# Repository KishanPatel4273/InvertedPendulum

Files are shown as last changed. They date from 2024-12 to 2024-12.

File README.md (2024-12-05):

# Inverted Pendulum on Cart

In InvertedPendulum.pdf lagrange mechanics is used to derive the dynamics of the system. Then A controller is designed.

## Materials

| Quantity | Item | Cost | 
|---|---|---|
| 12x | [100mm V Slot 2020 Aluminum](https://www.amazon.com/dp/B0B7DVN34Y?ref=ppx_yo2ov_dt_b_fed_asin_title&th=1) | 35.97 |
| 2x | [8mm x 400mm Aluminum rod](https://www.amazon.com/dp/B08JGD9F5P?ref=ppx_yo2ov_dt_b_fed_asin_title) | 11.99 |
| 4x | [8mm Aluminum rod support](https://www.amazon.com/dp/B0CWV45879?ref=ppx_yo2ov_dt_b_fed_asin_title&th=1) | 8.99  |
| 1x | [pulley system](https://www.amazon.com/dp/B07MF6TDHF?ref=ppx_yo2ov_dt_b_fed_asin_title) | 14.19 |
| 20x | [(8mm x 22mm x 7mm) (608 2RS) ball bearings](https://www.amazon.com/dp/B09PKD8QZZ?ref=ppx_yo2ov_dt_b_fed_asin_title&th=1) | 6.99  |
| 1x | [Stepper Motor](https://www.amazon.com/gp/product/B0B8HB5N4S/ref=ox_sc_saved_title_2?smid=AWQBCGWISS7BL&th=1) | 16.99
| 1x | [Rotary Encoder 600p/R](https://www.amazon.com/Taiss-Incremental-Encoder-Voltage-Warranty%EF%BC%89600P/dp/B07MX1SYXB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) | 18.99

| Quantity | Part
|---|---|
| 2x | [Cart.stl](/Model-V1/Cart.stl) |
| 1x | [Plate.stl](/Model-V1/Plate.stl) |
| 1x | [PulleyStand.stl](/Model-V1/PulleyStand.stl) |
| 1x | [BearingToPulleyPin.stl](/Model-V1/BearingToPulleyPin.stl) |
| 1x | [EncoderMount.stl](/Model-V1/EncoderMount.stl) |
| 1x | [PendulumMount.stl](/Model-V1/PendulumMount.stl) |
| 1x | [Pendulum.stl](/Model-V1/Pendulum.stl) |
| 1x | [StepperMotorMount.stl](/Model-V1/StepperMotorMount.stl) |
| 1x | [StepperMotorAdapter.stl](/Model-V1/StepperMotorAdapter.stl) |

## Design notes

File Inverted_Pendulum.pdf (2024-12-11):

# Inverted Pendulum

Kishan Patel

December 11, 2024

## 1 Introduction

## 2 Lagrange Mechanics

d
dt

∂L
∂q˙i

−

∂L
∂qi
= Fi with L = T − V | (1)

### 2.1 Finding the Lagrangian

T = Ttransitional + Trotational
= Tc + Tw + Twr

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
The velocity vectors are in reference to the center of gravity, I will assume that the density of each component is constant. Hence, the rod’s center of gravity is at 1
2

l and the weight’s, at the end of the rod, center of mass is at l.

vc =

x˙
0

vw =

x˙ + l

˙θ cos θ
−l

˙θ sin θ

| (3)

Velocity squared is v

2 = v · v

v

2
c = ˙x

2

v

2
w = ˙x

2 + 2lx˙

˙θcosθ + l

2 ˙θ
2

cos²
θ + l

2 ˙θ
2

sin²
θ

= ˙x

2 + 2lx˙

˙θcosθ + l

2 ˙θ
2

(4)

Now, simplify kinetic energy: T

T =

1
2

mcx˙

2

+

1
2

mwx˙

2 + mwlx˙

˙θcosθ +

1
2

mwl

2 ˙θ
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
[mc + mw] + lx˙

˙θ cos θmw +

1
2

l

2 ˙θ
2
[mw +

Iw
l

2

]

(5)

Now, will solve for the potential energy: V.

V = Vw
= mwgl(1 − cos θ)

(6)

Now, we can define the Lagrangian and solve for the mechanics with q1 = x, and q2 = θ.

L =

1
2

x˙

2

[mc + mw] + 1
2

l

2 ˙θ
2
[mw +

Iw
l

2

] + lx˙

˙θ cos(θ)mw − mwgl(1 − cos(θ))

=

1
2

x˙

2
[mc + mw] + l

2 ˙θ
2mw + lx˙

˙θ cos(θ)mw + mwgl cos(θ) − mwgl

(7)

q1 = x :

d
dt

∂L
∂x˙

=

∂L
∂x + Fx

d
dt( ˙x[mc + mw] + l mw

˙θ cos (θ)) = Fx

x¨[mc + mw] + lmw

¨θ cos(θ) − lmw
˙θ
2
sin(θ) = Fx

(8)

q1 = θ :

d
dt

∂L
∂ ˙θ

=

∂L
∂θ
d
dt(2 mw

˙θ l² + mw x˙ cos (θ) l) = −g l mw sin (θ) − l mw

˙θ x˙ sin (θ)

2mw

¨θl² + mwx¨ cos(θ)l − mwx˙

˙θ sin(θ)l = −g l mw sin (θ) − l mw

˙θ x˙ sin (θ)

2mw

¨θl² + mwx¨ cos(θ)l = −glmw sin(θ)

(9)

Since, the pendulum weight is being modeled as point mass Iw
l

2 = mw. sub in ¨x into ¨θ. Now, sub ¨θ back into ¨x Using Matlab syms to simplify even more.

x¨ =

2 l mw sin (θ)

˙θ
2 + 2 Fx + g mw cos (θ) sin (θ)

−mw cos (θ)

2 + 2 mc + 2 mw

¨θ = −

l mw cos (θ) sin (θ)

˙θ
2 + Fx cos (θ) + g mc sin (θ) + g mw sin (θ)

l

−mw cos (θ)

2 + 2 mc + 2 mw

(10)

To make the system more accurate, add friction terms −δcx˙ and −δp

˙θ to ¨x and ¨θ respectively.

## 3 State Space Formulation

Let x =

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
, and Fx = u | (11)

x˙ =

x˙
x¨
˙θ
¨θ

=

x2

2 l mw sin(x3) x4

2+2 u+g mw cos(x3) sin(x3) −mw cos(x3)

2+2 mc+2 mw
x4
−

l mw cos(x3) sin(x3) x4

2+u cos(x3)+g mc sin(x3)+g mw sin(x3) l(−mw cos(x3)

2+2 mc+2 mw)

= f(x, u) | (12)

### 3.1 linearization about fixed point

Now, find states to linearized at f(x, u) = 0

f(x, u) = 0

f([x1, 0, x3, 0]T
, 0) =

0

g mw cos(x3) sin(x3)
−mw cos(x3)

2+2 mc+2 mw
0
−

g mc sin(x3)+g mw sin(x3)
l(−mw cos(x3)

2+2 mc+2 mw)

(13)

f(x, u) = 0 when x1 ∈ R, x2 = 0, x3 = πn ∀n ∈ Z, x4 = 0, and u = 0.

x¯ =

x1
0
πn = 0
0

(14)

Now, we are ready for the state space equation ˙x = Ax + Bu. To find the matrices A and B we will take the Jacobian of f(x, u). For the model, we will want x3 to be 0 as that is the upright position of the pendulum.

x˙ = ∂xf

[x1,0,0,0]T ,0

(x − x¯) + ∂uf

[x1,0,0,0]T ,0

(u − 0)

x˙ =

0 | 1 | 0 | 0
0 −δ
| | g mw 2 mc+mw | 0
0 | 0 | 0 | 1
0 −δ −
| | g mc+g mw l (2 mc+mw) | 0

(x − x¯) +

0
2
2 mc+mw
0
−

1
l (2 mc+mw)

u

y = Cx

(15)

Now, we have our state space equation and measurement equation. The δ term is friction of the cart moving horizontally.

### 3.2 Controllability

The rank(-

B AB A²B A³B
) = 4; therefore, we have full controllability of the system with our control Fx = u.

### 3.3 Observability

C =

1 0 0 0
(16)

To actualize the system, I will take the simplest case where the sensors will capture the positional state x1 = x only. Now calculate the rank Observability matrix to see if the system is full state observable from just the position of the cart.

O =

C

T AT C

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
(17)

The rank of the Observability matrix is 4; therefore, we can estimate all the other states.

## 4 Controller with C = I

### 4.1 Proportional Control

For the proportional control let u − u¯ = −K(x − x¯).

x˙ = Ax + Bu
x˙ = Ax − BKx
x˙ = (A − BK)x

(18)

Since the system is controllable, the matrix K can be placed so that A − BK can have any eigenvalues. Now what eigenvalues should one choose? λi ∈ {z ∈ C : Re(z) < 0}. But, what is the optimal choice? For this, the Linear Quadratic Regulator (L.Q.R.) will be used. Define the cost J which is a quadratic function in x and u.

J =

Z ∞

0

x

T Qx + u

T Ru dt

x˙ = Ax + Bu

Q =

1 | 0 | 0 | 0
0 10 | 0 | 0
0 | 0 | 10 | 0
0 | 0 | 0 | 100

R =

1

(19)

Now finding the minimum of the cost function is all done for us in Matlab. Kr = lqr(A, B, Q, R). The interpretation of Q and R is that it defines the cost of controlling specific states.

### 4.2 Integral Control

For the proportional control let u − u¯ = −KI

R t
0

(x − x¯)dt.

w =

Z t

0

(x − x¯)dt

w˙ = x − x¯
w(0) = 0

(20)

To implement integral action set up a new state w which will update with the following discrete rule wn = wn−1 + ˙wndt. The internal gain KI = [.1, .1, .1, .1].

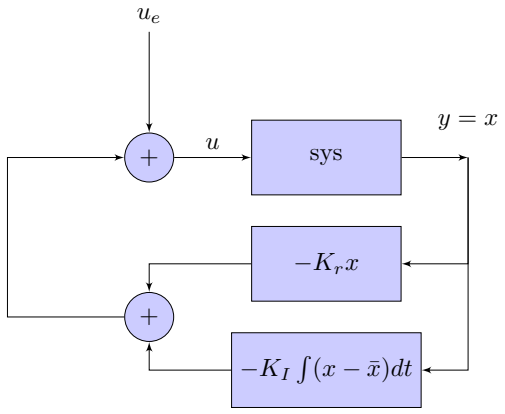
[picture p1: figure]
sys; −Krx

## 5 Controller with C =

1 0 0 0

Since the controller has access to only the positional state, an estimator must be built to estimate other states.

### 5.1 Estimator

A system needs to build that will give us ˆx. The estimate ˆx needs to approach the actual state x. So the error e = x − xˆ needs to approach 0.

e = x − xˆ
e˙ = ˙x − ˙xˆ

e˙ = Ax + Bu − (Axˆ + Bu + f) e˙ = A(x − xˆ) − L(y − yˆ)
e˙ = (A − LC)e

(21)

So if L can be placed such that A − LC has negative eigenvalues, then the estimator will approach the actual state, that is, if the observability matrix has full rank.

˙xˆ = Axˆ + Bu + L(y − yˆ)

yˆ = Cxˆ

(22)

### 5.2 Kalman Filter

The matrix L needs to be chosen optimally to make the estimator. Let Vd be the covariance matrix for the disturbance in the system, and let Ln be the covariance matrix for the noise in the measurement.

x˙ = Ax + Bu + wd
(23)

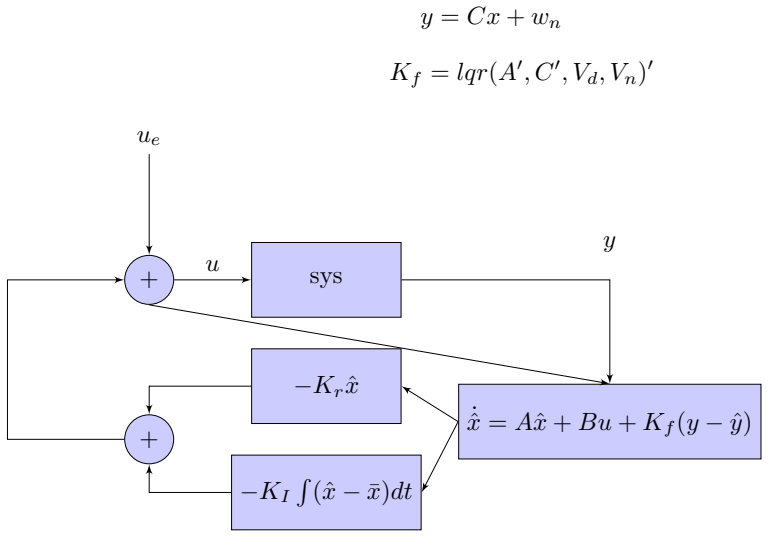
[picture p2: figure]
Kf = lqr(A; sys; −Krxˆ; ˙xˆ = Axˆ + Bu + Kf (y − yˆ)

(24)

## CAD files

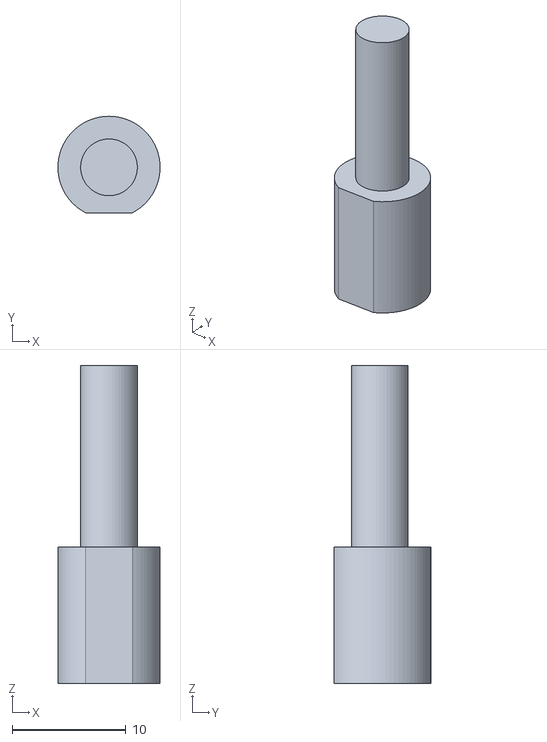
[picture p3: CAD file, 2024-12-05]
Model-V1/StepperMotorAdapter.stl
9.00 x 8.50 x 28.0

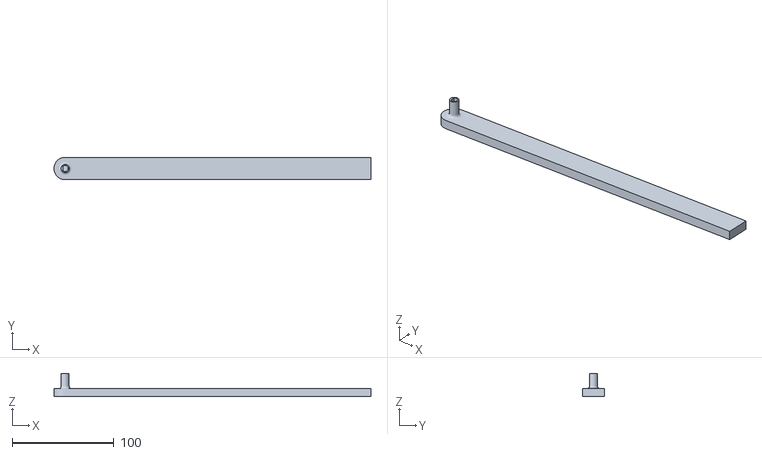
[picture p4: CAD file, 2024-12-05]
Model-V1/Pendulum.stl
311.0 x 22.0 x 23.0

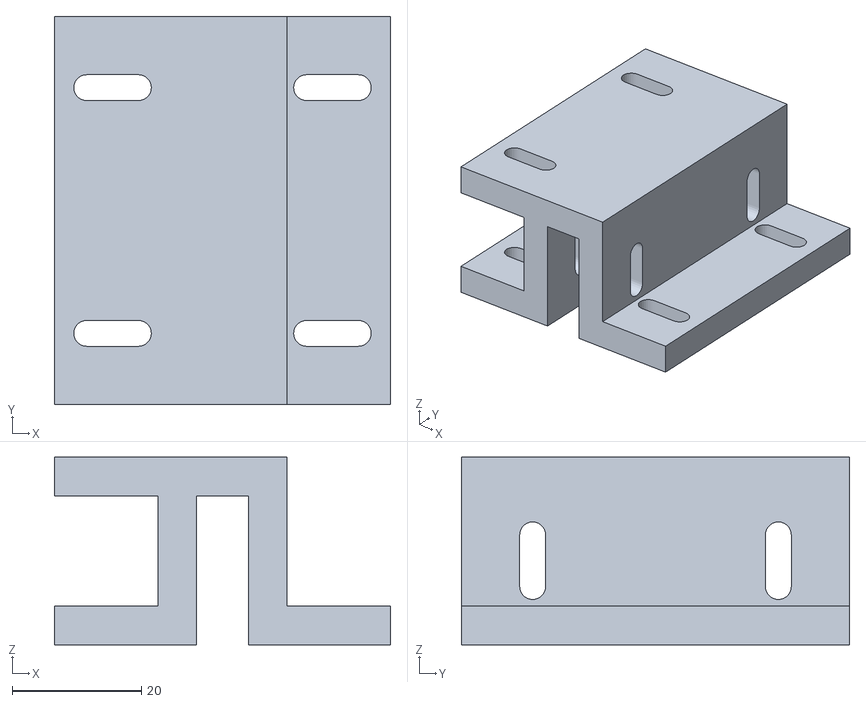
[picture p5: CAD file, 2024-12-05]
Model-V1/Cart.stl
52.0 x 60.0 x 29.0

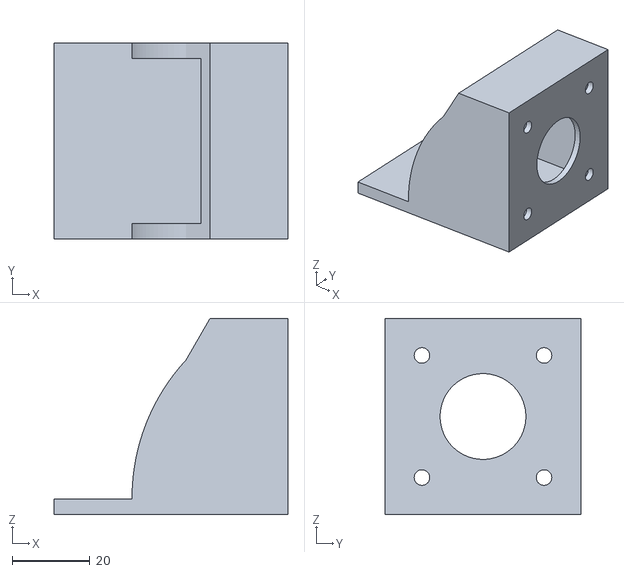
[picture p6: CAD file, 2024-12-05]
Model-V1/StepperMotorMount.stl
60.0 x 50.3 x 50.3

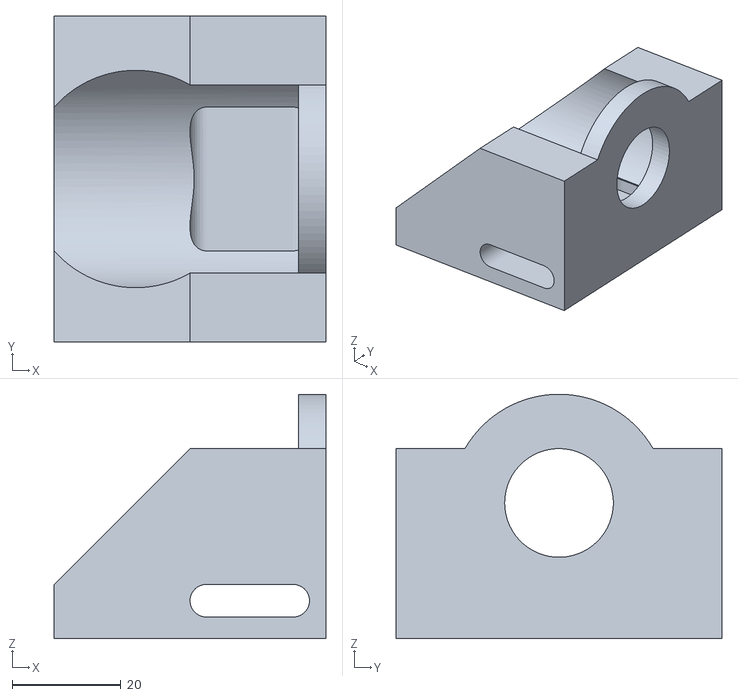
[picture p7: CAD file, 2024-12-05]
Model-V1/EncoderMount.stl
50.0 x 60.0 x 45.0

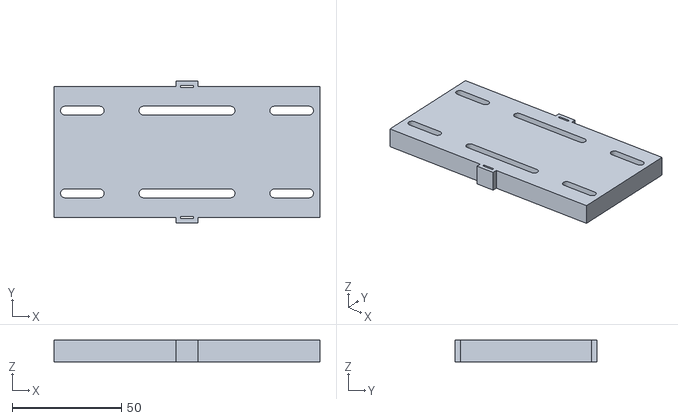
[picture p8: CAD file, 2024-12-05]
Model-V1/Plate.stl
122.0 x 65.0 x 10.0

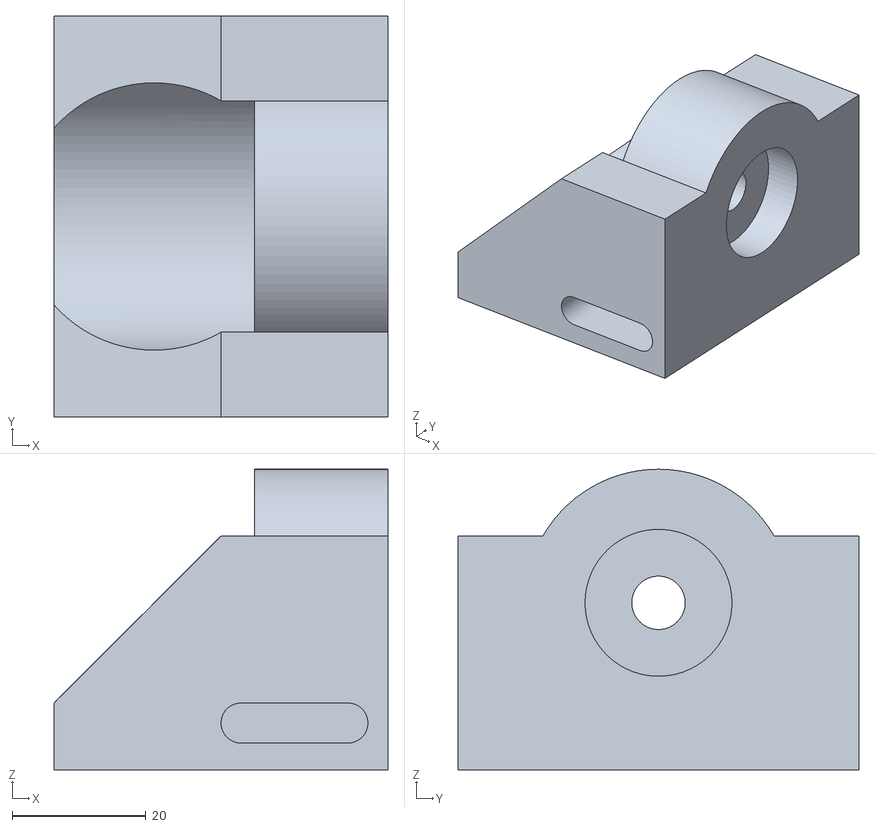
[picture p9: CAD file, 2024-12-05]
Model-V1/PendulumMount.stl
50.0 x 60.0 x 45.0

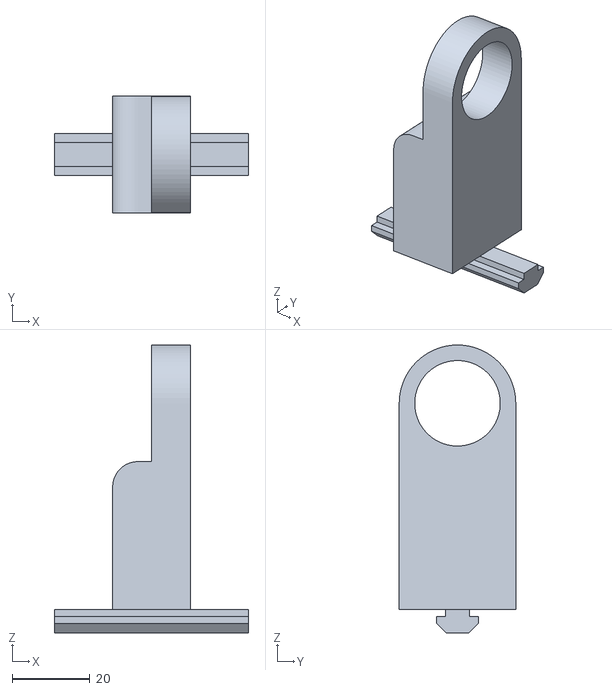
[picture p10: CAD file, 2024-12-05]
Model-V1/PulleyStand.stl
50.0 x 30.0 x 74.1

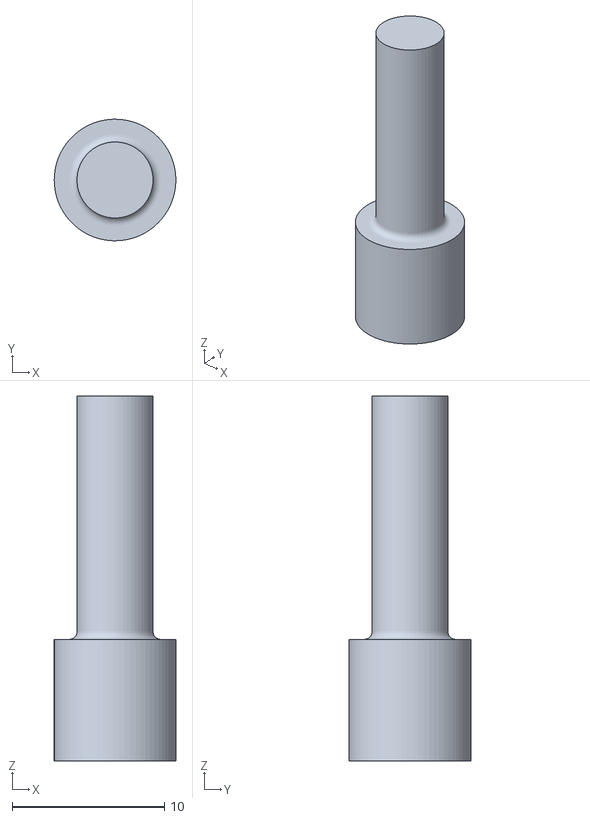
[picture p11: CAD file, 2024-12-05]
Model-V1/BearingToPulleyPin.stl
8.00 x 8.00 x 24.0

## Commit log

2024-12-05 stl files for custom parts
    [BearingToPulleyPin.stl, Cart.stl, EncoderMount.stl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]
2024-12-05 stl files
    [BearingToPulleyPin.stl, Cart.stl, EncoderMount.stl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]
